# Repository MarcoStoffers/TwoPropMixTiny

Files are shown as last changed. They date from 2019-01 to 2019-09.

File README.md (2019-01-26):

# TwoPropMixTiny
## 2-prop mixer for RC model with 2 drive props, rudder and bow thruster
TwoPropMixTiny

- Depending on the direction, the curve inner motor is braked or controlled to reverse (adjustable via a setup). The sensitivity at which curve position the mixer should intervene can be set via a potentiometer.
- If a bow thruster is also used, this can also be used to support cornering (can also be switched on via setup). Up to which speed the bow thruster intervenes can be adjusted with the 2nd potentiometer.

## Requirement
- All motors (right-hand drive, left-hand drive, bow thruster) must have their own speed controller and the two drives must run equally (the model does not pull away to one side when driving straight ahead).
- The model can be "normally" driven via an RC remote control (Forward | Reverse | Left | Right | Bow Thruster Left | Bow Thruster Right)
- The power supply for the module (4.5V - 5.5V) is guaranteed (see manual / only german at the moment).

## Base
The module is based on a microchip ATtiny841 which is programmed via the [Arduino IDE](https://arduino.cc/). To use the microcontroller, the extension of [Spence Konde](https://github.com/SpenceKonde/ATTinyCore) is necessary. Programming is done without a bootloader directly via the ISP contacts on the bottom side of the PCB with an AVR programmer.

## License
The project is licensed under the Creative Common License. A rebuild for private or non-profit associations is desired, commercial rebuild or distribution I forbid. If someone should develop the mixer further, I ask for the naming of the original project.

CreativeCommonLicense

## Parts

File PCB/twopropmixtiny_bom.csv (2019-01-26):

Qty | Value | Device | Package | Parts | Description
8 |  | JP2EJP2_OHNE_TEXT | JP2 | JP1, JP2, JP3, JP4, JP5, JP6, JP7, JP8 | JUMPER
1 |  | LEDCHIPLED_0805 | CHIPLED_0805 | LED1 | LED
3 |  | SJ | SJ | SJ1, SJ2, SJ3 | SMD solder JUMPER
2 |  | TRIM_EU-PT10 | PT-10 | R17, R18 | POTENTIOMETER
1 | 100nF | C-EUC0805 | C0805 | C1 | CAPACITOR, European symbol
1 | 100µF / 16V | CPOL-EUD | PANASONIC_D | C2 | POLARIZED CAPACITOR, European symbol
9 | 10k | R-EU_R0805 | R0805 | R1, R9, R10, R11, R12, R13, R14, R15, R16 | RESISTOR, European symbol
5 | 1k | R-EU_R0805 | R0805 | R2, R3, R6, R7, R8 | RESISTOR, European symbol
1 | ATtiny841-SSU | TINY24/44/84-SSU | SOIC14 | IC2
4 | IRLML2502 | IRLML2502 | SOT23-3 | Q1, Q2, Q3, Q4 | International Rectifier
1 | ISP | ISP | ISP | U$1
1 | POLOLU2121 | POLOLU2121 | POLOLU2121 | IC1

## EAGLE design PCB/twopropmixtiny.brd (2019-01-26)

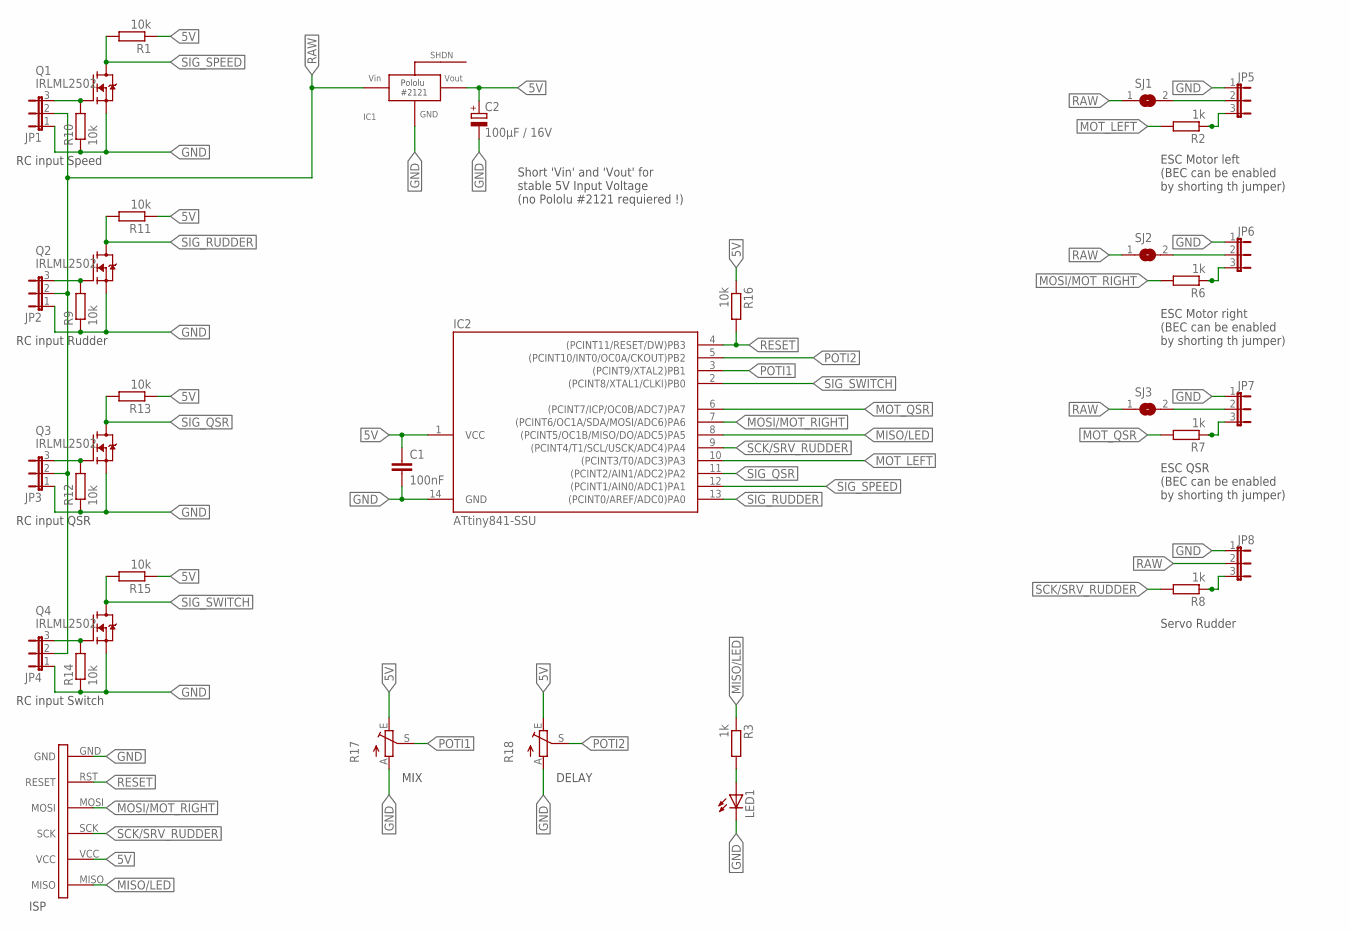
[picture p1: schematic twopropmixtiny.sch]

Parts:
C1: 100nF; C0805
C2: 100µF / 16V; PANASONIC_D
IC1: POLOLU2121
IC2: ATtiny841-SSU; SOIC14
JP1, JP2, JP3, JP4, JP5, JP6, JP7, JP8: JP2EJP2_OHNE_TEXT; JP2
LED1: LEDCHIPLED_0805; CHIPLED_0805
Q1, Q2, Q3, Q4: IRLML2502; SOT23-3
R1, R9, R10, R11, R12, R13, R14, R15, R16: 10k; R0805
R2, R3, R6, R7, R8: 1k; R0805
R17, R18: TRIM_EU-PT10; PT-10
SJ1, SJ2, SJ3: SJ
U$1: ISP

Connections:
5V: C1.1, C2.+, IC1.VOUT, IC2.1 (VCC), R1.1, R11.1, R13.1, R15.1, R16.1, R17.E, R18.E, U$1.VCC
GND: C1.2, C2.-, IC1.GND, IC2.14 (GND), JP1.1, JP2.1, JP3.1, JP4.1, JP5.1, JP6.1, JP7.1, JP8.1, LED1.C, Q1.2 (S), Q2.2 (S), Q3.2 (S), Q4.2 (S), R9.1, R10.1, R12.1, R14.1, R17.A, R18.A, U$1.GND
MISO/LED: IC2.8 ((PCINT5/OC1B/MISO/DO/ADC5)PA5), R3.1, U$1.MISO
MOSI/MOT_RIGHT: IC2.7 ((PCINT6/OC1A/SDA/MOSI/ADC6)PA6), R6.2, U$1.MOSI
MOT_LEFT: IC2.10 ((PCINT3/T0/ADC3)PA3), R2.2
MOT_QSR: IC2.6 ((PCINT7/ICP/OC0B/ADC7)PA7), R7.2
unnamed: JP1.3, Q1.1 (G), R10.2
unnamed: JP5.3, R2.1
unnamed: JP2.3, Q2.1 (G), R9.2
unnamed: LED1.A, R3.2
unnamed: JP3.3, Q3.1 (G), R12.2
unnamed: JP6.3, R6.1
unnamed: JP7.3, R7.1
unnamed: JP8.3, R8.1
unnamed: JP5.2, SJ1.2
unnamed: JP6.2, SJ2.2
unnamed: JP7.2, SJ3.2
unnamed: JP4.3, Q4.1 (G), R14.2
POTI1: IC2.3 ((PCINT9/XTAL2)PB1), R17.S
POTI2: IC2.5 ((PCINT10/INT0/OC0A/CKOUT)PB2), R18.S
RAW: IC1.VIN, JP1.2, JP2.2, JP3.2, JP4.2, JP8.2, SJ1.1, SJ2.1, SJ3.1
RESET: IC2.4 ((PCINT11/RESET/DW)PB3), R16.2, U$1.RST (RESET)
SCK/SRV_RUDDER: IC2.9 ((PCINT4/T1/SCL/USCK/ADC4)PA4), R8.2, U$1.SCK
SIG_QSR: IC2.11 ((PCINT2/AIN1/ADC2)PA2), Q3.3 (D), R13.2
SIG_RUDDER: IC2.13 ((PCINT0/AREF/ADC0)PA0), Q2.3 (D), R11.2
SIG_SPEED: IC2.12 ((PCINT1/AIN0/ADC1)PA1), Q1.3 (D), R1.2
SIG_SWITCH: IC2.2 ((PCINT8/XTAL1/CLKI)PB0), Q4.3 (D), R15.2

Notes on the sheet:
RC input Speed
RC input Rudder
RC input QSR
RC input Switch
ISP
Short 'Vin' and 'Vout' for stable 5V Input Voltage (no Pololu #2121 requiered !)
MIX
DELAY
ESC Motor left (BEC can be enabled by shorting th jumper)
ESC Motor right (BEC can be enabled by shorting th jumper)
ESC QSR (BEC can be enabled by shorting th jumper)
Servo Rudder

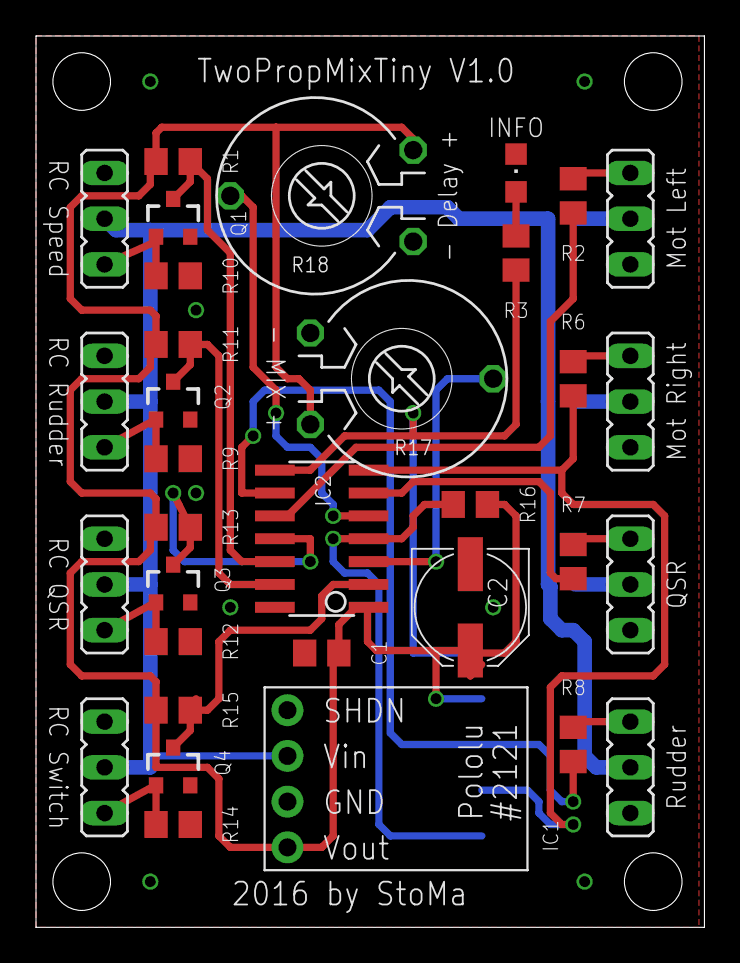
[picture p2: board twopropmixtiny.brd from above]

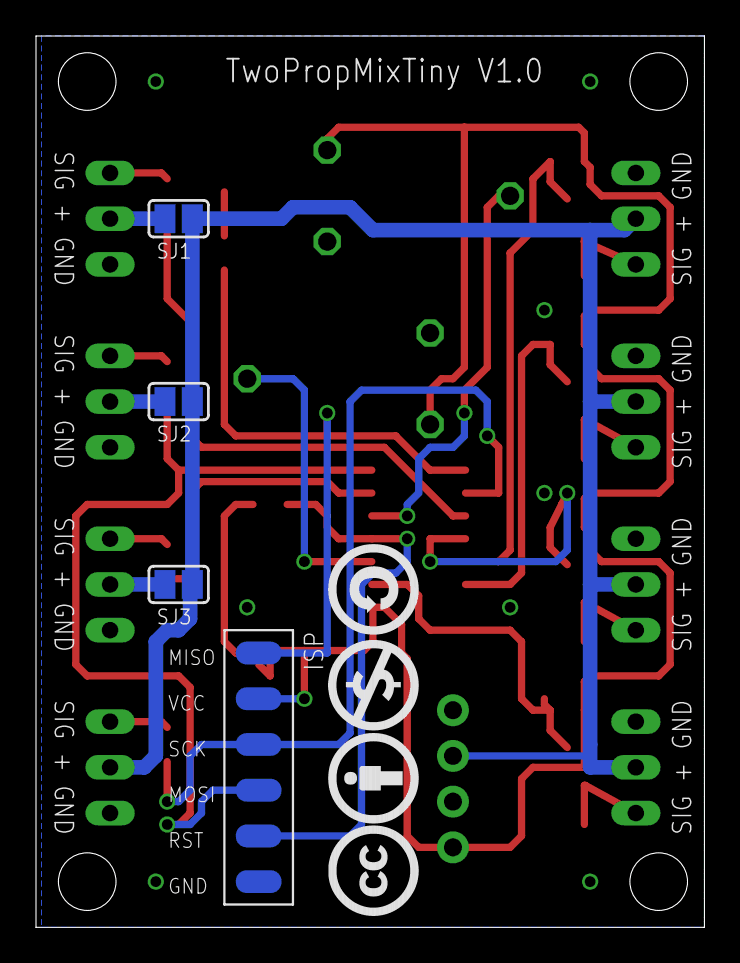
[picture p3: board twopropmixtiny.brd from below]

Board: 2 copper layers, 37.1 x 49.5 mm, 37 parts (4 on the bottom side), 27 nets.

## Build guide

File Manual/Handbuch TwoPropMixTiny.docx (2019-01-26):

Handbuch

TwoPropMixTiny

Version 1.0

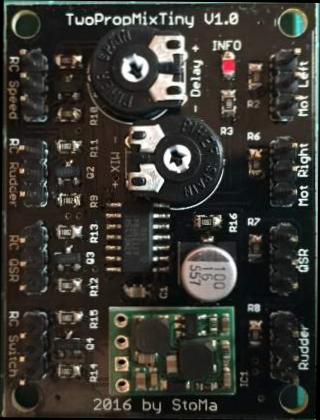
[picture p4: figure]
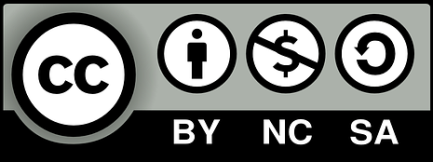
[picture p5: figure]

Inhalt

- Funktion und Einsatzzweck ……………………………………………………………….. Seite 3
- Vorgaben auf Sender & Empfängerseite …………………………………………. Seite 3
- Stromversorgung und Inbetriebnahme ………………………………………..... Seite 4
- Einstellungen und Kalibrieren …………………………………………………………. Seite 6
- Funktion im fahrenden Modell ……………………………………………………….. Seite 7
- Besonderheiten ………………………………………………………………………………… Seite 8

Begriffe und Abkürzungen die in diesem Handbuch verwendet werden:

- QSR (Querstrahlruder) : Quer-Antrieb im Bug eines Schiffes zum besseren Manövrieren
- Schrauben : Antriebsschrauben unter dem Modell
- Motoren : Antriebsmotoren / Elektromotoren
- Brushed / Brushless : Bürstenmotor (herkömmliche Bauweise) / Bürstenloser Motor
- Regler : Fahrtregler (genauer: Fahrtsteller) der die Elektromotoren ansteuert
- FS (Fernsteuerung/Sender) : Funkfernsteuerung mit mind. 4 Kanälen
- BB / ST (Backbord / Steuerbord) : Richtung im Schiffsverkehr (BB = links & ST = rechts)
- BEC : Stromversorgung des Empfängers im Modell über einen Fahrtregler
- UBEC : getrennte, geregelte Stromversorgung des Empfängers aus einem separaten Akku

Funktion und Einsatzzweck

Der TwoPropMixTiny stellt einen Mischer für 2 Antriebsmotoren, einem Querstrahlruder und einem oder mehrere Ruder dar. Über das Setup sind verschiedene Einstellungen zur Anpassung an das Modell möglich und über die beiden Drehregler auf der Platine kann man die Verzögerung (ab welcher Ruderlage soll das Mischen erfolgen) und Mischung (bis zu welcher Geschwindigkeit – abhängig vom Gashebel – soll das Querstrahlruder mit eingemischt werden) jederzeit verändern (auch bei eingeschalteten Modell!).

Die Mischung der 2 Antriebsmotoren und wahlweise des Querstrahlruders ist hilfreich, um große, lange Modelle eine bessere Manövrier-Eigenschaft zu geben. Dazu wird der kurveninnere Motor gedrosselt bis zum Stillstand oder sogar in der Drehrichtung umgedreht (abhängig von den Einstellungen). Diese Drosselung erfolgt proportional zur Ruderlage. Das bedeutet: bisschen Ruder Backbord – Backbord Motor wird ein wenig gedrosselt. Hart Ruder Backbord – Backbord Motor wird gestoppt oder läuft 50% rückwärts.

Zusätzlich kann das Querstrahlruder bis zu einer eingestellten Motor Leistung mit zugemischt werden. Gerade beim Manövrieren in einer Hafenanlage oder bei Anlegen am Kai ist diese Funktion sehr hilfreich. Ist die Funktion abgeschaltet (über den Schalteingang auch über die Fernsteuerung zu- und abschaltbar) wird das Querstrahlruder wie gewohnt mit dem Geber an der Fernsteuerung geregelt.

Wird keine Fahrt vorwärts oder rückwärts über den Gas Hebel an der Fernsteuerung gegeben, kann man mit dem Betätigen des Ruder Hebels ein Drehen des Modells erreichen („Drehen auf dem Teller“). Dieses erfolgt durch gegenseitiges Drehen der Antriebsschrauben und mit Querstrahlruder Unterstützung, wenn die Funktion aktiviert wurde. Auch hier folgt die Drehzahl der Motoren dem Ruderausschlag / Hebelstellung am Sender.

Vorgaben auf Sender & Empfängerseite

Folgende Vorgaben sind mit der Verwendung des TwoPropMixTiny einzuhalten:

- Jeder Motor/QSR hat seinen eigenen Regler und ist funktionsfähig
- Die verbauten Servos sind Standard und keine BUS-Servos (z.B. S-bus von Futaba)
- Der Empfänger wird mit einer Spannung zwischen 4-12V, über das BEC eines Fahrtreglers oder ein gesondertes UBEC betrieben
- Idealerweise sind die Kanäle für Motor, Servo und QSR auf der Senderseite nicht auf Reverse geschaltet

Stromversorgung und Inbetriebnahme

Achtung ! Dieser Abschnitt ist extrem wichtig, da bei einer falschen Stromversorgung der TwoPropMixTiny Schaden nehmen kann. Lesen Sie daher den folgenden Abschnitt genau durch!

Der TwoPropMixTiny wird mit dem Empfänger verbunden und bezieht daher auch seinen Strom. Daher müssen wir anhand der Stromversorgung des Empfängers entscheiden, welche Maßnahmen für die Inbetriebnahme am TwoPropMixTiny nötig sind.

1. Der Empfänger wird über einen der Fahrtregler mit Strom versorgt - BEC (5V) :

Hierzu muss auf der Unterseite der Platine des Mischers eine der Stromversorgungsbrücken SJ1 – SJ3 mit Hilfe eines Lötkolbens und Lot geschlossen werden.

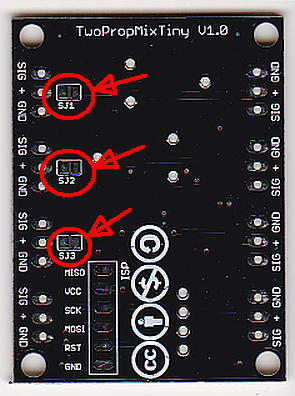
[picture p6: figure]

Soll die Stromversorgung über den Regler

des BB Motors erfolgen, ist SJ1 zu

schließen.

Für den Regler des ST Motors ist

SJ2 zu schließen.

Für den Regler des QSR ist SJ3 zu schließen

Zusätzlich muss auf der Vorderseite eine Kabel-

Brücke eingelötet werden. Im Feld „Pololu

#2121“ sind die beiden Kontakte „Vin“ und

„Vout“ mit einem kleinen Stück Kabel zu

verbinden.

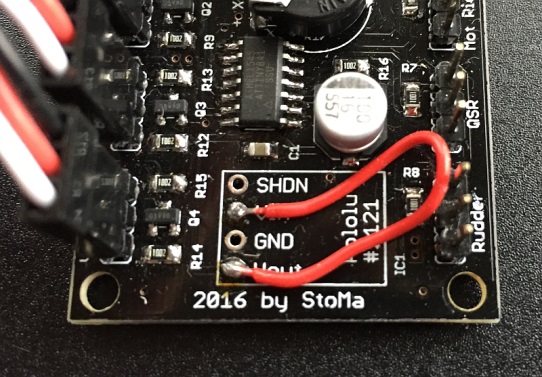
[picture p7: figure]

ACHTUNG ! Gibt das BEC des Fahrtreglers mehr als 5,5V aus muss Variante 3 gewählt werden !

2. Der Empfänger wird mit einem separaten UBEC mit Strom versorgt:

Hierzu bleiben die Brücken SJ1 – SJ3 auf der Unterseite des Mischers offen. Die Kabelbrücke muss auch hier eingelötet werden

ACHTUNG ! Gibt das externe UBEC mehr als 5,5V aus muss Variante 3 gewählt werden !

3. Der Empfänger wird mit einem separaten Akku oder einem (U)BEC mit mehr als 5,5V betrieben:

Hier bleiben die Brücken auf der Unterseite der Platine ebenfalls geöffnet. Zusätzlich wird ein Spannungsregler vom Typ Pololu #2121 benötigt. Dieser ist über die einschlägigen Onlineshops oder Auktionsportale zu beziehen.

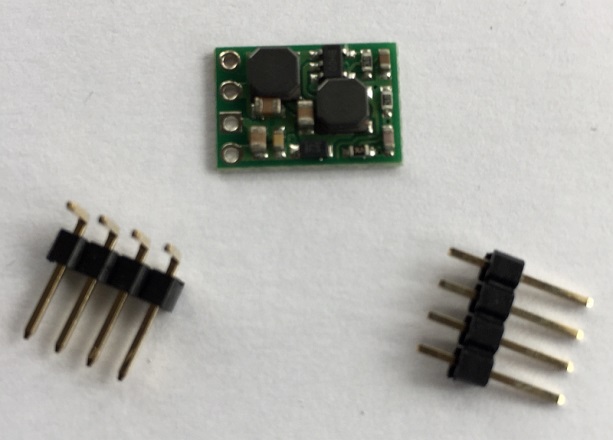
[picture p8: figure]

Zur Montage wird die abgewinkelte Stiftleiste mit dem langen Ende von unten durch die Platine gesteckt und der Spannungsregler von oben aufgesteckt und verlötet

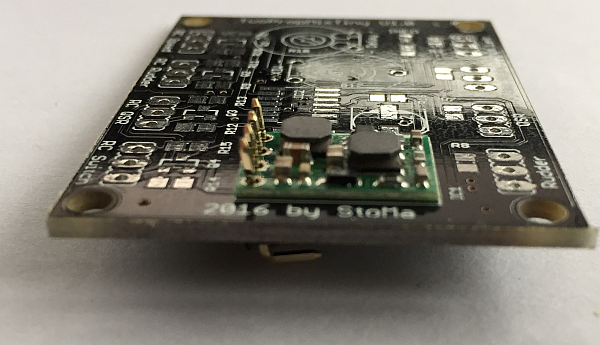
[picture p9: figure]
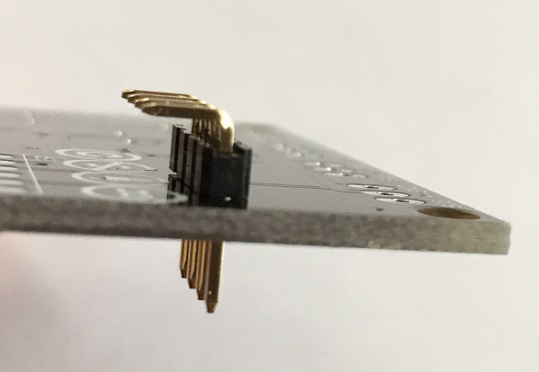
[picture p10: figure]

Die überstehenden Kontakte dann bitte mit einem feinen Seitenschneider entfernen oder zumindest isolieren. Mit diesem Modul kann der Empfänger mit nachgeschalteten TwoPropMixTiny zwischen 4V und 12V betrieben werden.

Inbetriebnahme

Für den Anschluss des Mischers an den Empfänger eignen sich kurze Anschlusskabel für Servos in der Länge 10cm. Die Belegung der Servokabel ist wie folgt:

- Schwarz = Minus (GND)
- Rot = Plus (+)
- Weiß = Signal (SIG)

Die Pinbelegung ist auf der Unterseite der Platine aufgedruckt. Der entspr. Eingang ist wiederrum aus Platzgründen auf der Oberseite aufgedruckt.

- Der Eingang „RC Rudder“ wird an dem Empfänger Port für das Ruder angeschlossen. Der Servo für das Ruder wird am Ausgang „Rudder“ eingesteckt.
- Der Motoranschluss vom Empfänger kommt an „RC Speed“ und die beiden Fahrtregler der Motoren an „Mot Left“ bzw. „Mot Right“.
- Empfängerausgang für das QSR kommt an „RC QSR“ und der Regler vom QSR an den Ausgang „QSR“

Der Anschluss „RC Schwitch“ ist etwas Besonderes. Man kann Ihn entweder über einen Schaltkanal direkt mit dem Empfänger verbinden oder den Pin „SIG“ an einem Multiswitch Port schalten (gegen Minus (GND) schalten). Welchen Typ von Eingang der „RC Switch“ Port erhalten soll, wird im Setup eingestellt!

Einstellungen und Kalibrieren

Um den TwoPropMixTiny an das jeweilige Modell und Fernsteuerung anzupassen gibt es ein Setup welches mit dem Hebel an der Fernsteuerung für den Motor und der „Info“ LED auf der Platine durchgeführt wird. Zur Vorsicht bitte das Setup nur mit nicht angesteckten Fahrtenregler und Servo vornehmen. Die Ausgabe der Signale ist zwar deaktiviert aber einige Fahrtregler interpretieren das fehlende Signal als Failsafe und gehen dann gerne mal in eine Vollgas Stellung.

Das Setup geschieht folgendermaßen:

- Beim Einschalten des Empfängers den Knüppel für den Motor am Sender auf Vollgas vorwärts stellen und halten (ist hier ein Reverse programmiert natürlich auf rückwärts)
- Die LED auf dem Mischer blinkt 1x
- Hebel wieder in Mittelstellung -> die LED blinkt noch einmal kurz auf
- Wenn der Hebel jetzt wieder auf Vollgas vorwärts gebracht wird, ist der Schaltkanal für das Zuschalten der QSR Unterstützung, als RC-Eingang programmiert. Wird der Hebel auf Vollgas rückwärts gestellt, ist der Schaltkanal ein normaler Schalteingang, welcher mit einem Schaltmodul oder Multiswitch beschaltet werden muss -> zur Bestätigung blinkt die LED 2x
- Hebel wieder in Mittelstellung -> die LED blinkt einmal kurz auf
- Beim nächsten Schritt wird per „vorwärts“ Richtung des Hebels der Enhanced Mode aktiviert, bei dem der Kurven innere Motor nicht nur bis zum Stillstand sondern bis 50% Rückwärtsfahrt angesteuert wird. Hebel rückwärts deaktiviert den Enhanced Mode -> zur Bestätigung blinkt die LED 3x
- Hebel wieder in Mittelstellung -> die LED blinkt einmal kurz auf
- Im letzten Schritt kann man den Mischer mit „Hebel vorwärts“ in den Reverse Mode versetzen. Damit werden die Motoren vertauscht und das QSR dreht in die andere Richtung. Dieses wird benötigt wenn an der Fernsteuerung Kanäle auf reverse geschaltet werden mussten, da der Einbau von z.B. Ruderservo nicht anders möglich war. „Hebel rückwärts“ übernimmt den Standard Mode. -> zur Bestätigung blinkt die LED 4x
- Hebel wieder in Mittelstellung -> die LED blinkt einmal kurz auf
- Das Setup ist abgeschlossen und der Mischer läuft normal los

Um den Mischer an die unterschiedlichen Fernsteuerungen anzupassen, gibt es eine Kalibrierung. Dazu den Empfänger wieder ausschalten, den Motor Hebel an der Fernsteuerung auf Vollgas rückwärts bringen und den Empfänger wieder einschalten. Die „Info“ LED auf dem TwoPropMixTiny blinkt nun dauerhaft für etwa eine Minute. In dieser Minute müssen die verwendeten Hebel an der Fernsteuerung für Motor, Lenkung, QSR und wenn programmiert auch den Schalteingang auf Maximum und Minimum gebracht werden. Also am besten mit dem Motorhebel anfangen:

Max, 1s warten, Min, 1s warten – weiter zur Lenkung: Max, 1s warten, Min, 1s warten und so weiter. Dieser Vorgang kann jederzeit wiederholt werden. Nach dem Blinken der LED werden die Werte in den internen Speicher vom Mischer abgelegt. Auch die Einstellungen aus dem Setup werden dauerhaft gespeichert, können aber jederzeit wieder geändert werden in dem das Setup wiederholt wird.

Die Einstellung der beiden Drehregler für „Delay“ – ab welcher Ruderlage das Abbremsen des kurveninneren Motors erfolgen soll – und „Mix“ – bis zu welcher Geschwindigkeit das QSR mit dazu gemischt werden soll – nimmt man am Besten im fahrbereiten Modell vor. Für die Verstellung der Drehregler eignet sich ein billiger Phasenprüfer aus dem Baumarkt.

Funktionen im fahrenden Modell

Der TwoPropMixTiny unterstützt die Fahrfunktion im Modell bei unterschiedlichen Situationen

- Fahrt voraus ohne QSR Unterstützung

Bei Fahrt voraus (vorwärts) wird ab der eingestellten Verzögerung der Ruderlage (Drehregler „Delay“) der kurveninnere Motor gedrosselt bis er bei hart Ruder zum Stillstand / 50% rückwärts dreht (je nach Einstellung im Setup). Dadurch ist ein großes, langes Modell besser zu manövrieren.

Ist der Drehregler „Delay“ auf Vollanschlag „+“ ist diese Funktion deaktiviert!

- Fahrt voraus mit QSR Unterstützung

Ist die QSR Unterstützung aktiv, wird bis zu der eingestellten Gashebel-Position (über den Drehregler „Mix“) das QSR je nach Ruderlage bi zur maximalen Drehzahl bei hart Ruder zu gemischt. Auf die Funktion für das verlangsamen der kurveninneren Schraube hat dies keinen Einfluss.

Ist der Drehregler „Mix“ auf Vollanschlag „+“ läuft das QSR bei dieser Funktion in jeder Kurvenfahrt mit!

- Fahrt achtern ohne QSR Unterstützung

Die Rückwärtsfahrt wird nicht beeinflusst. Die beiden Antriebsmotoren laufen 1:1 analog zum Gashebel an der Fernsteuerung

- Fahrt achtern mit QSR Unterstützung

Auch hier wird nur die QSR Unterstützung hinzugeschaltet. Andere Funktionen bleiben erhalten.

- Betätigung des Ruder-Hebels bei stehenden Modell ohne QSR Unterstützung

Wird bei stehenden Modell der Ruder-Hebel bewegt, werden die Antriebsmotoren gegenläufig angesteuert (vorwärts & rückwärts) so dass sich das Modell auf der Stelle dreht. Die Geschwindigkeit der Motoren ist abhängig von der Ruderlage – bei hart Ruder drehen die Motoren mit der maximalen Drehzahl

- Betätigung des Ruder-Hebels bei stehenden Modell mit QSR Unterstützung

Gleiche Funktion wie oben nur durch die Unterstützung mit dem QSR dreht das Modell quasi auf dem Teller (Drehachse ist mittig vom Schiff – nicht achtern).

Besonderheiten

Es gibt ein paar Punkte die man bei dem Einsatz des TwoPropMixTiny wissen sollte:

- Nach dem Einschalten des Empfängers wird erst auf gültige Werte gewartet biss der Start des Mischers erfolgt. Dies ist für den Einsatz des TwoPropMixTiny mit einem 2.4GHz Empfänger wichtig, da hier erst noch die Verbindung zum Sender hergestellt werden muss (Binding) was gerne mal 1-2 s dauert.
- Nach dem Start des Mischers werden von den Eingängen „RC Speed“, „RC Rudder“ & „RC QSR“ die Mittelstellung übernommen. Verwendet man am Sender für diese Kanäle einen Hebel, der nicht automatisch in die Mittelstellung zurück geht (nicht selbst neutralisierender Hebel / Ratsche), wird die zuletzt eingestellte Position als Mittelstellung gespeichert. Hier hilft dann nur ein Neustart durch Aus- und wieder Einschalten des Modells bei korrigierter Hebelstellung!
- Verwendet man Fahrtregler, die bei Rückwärtsfahrt nur 50% Leistung ausgeben, um das Modell nicht unter Wasser zu ziehen, wird das Modell nicht auf der Stelle drehen können.

Auch ist der Effekt im Enhanced Mode nicht so stark wie bei voller Leistung rückwärts.

- Bei der Verwendung von Brushless Motoren ist der Start des Motors meist recht ruckig. Hier sollte der Enhanced Mode – also das rückwärts drehen des kurveninneren Motors – nicht aktiviert werden, da es sonst zu unschönen Fahrmanövern kommt.

Marco Stoffers Handbuch TwoPropMixTiny 11/2016

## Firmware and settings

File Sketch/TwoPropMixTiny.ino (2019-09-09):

/* ==========================================================================
**  TwoPropMixTiny V1.1 
**
**  Core: ATtiny841 / Dr.Azzy (http://drazzy.com/e/tiny841.shtml9)
**
** Setup:
** ------
** 1) Motor stick in max up-position and switch on -> wait for long LED blink
** 2) Motor stick in center-position -> wait for LED blink
** 3) Motor stick in up-position for RC Switch input or down-position for Switch input via Multiswitch -> wait for double LED blink
** 4) Motor stick in center-position -> wait for LED blink
** 5) Motor stick in up-position for Enhanced mode on or down-position for Enhanced mode off -> wait for tripple LED blink
** 6) Motor stick in center-position -> wait for LED blink
** 7) Motor stick in up-position for Reverse mode or down-position for Normal mode -> wait for 4 times LED blink
** 8) Motor stick in center-position -> wait for long LED blink
** Done !
**
** Calibration: 
** ------------
** 1) Motor stick in max down-position and switch on -> wait for LED permanent blinking (1min)
** 2) Put all sticks to their maximum and minimum positions one after another until LED blinking stops
** Done !
**
**  D3 : QSR Output
**  D4 : Motor right Output
**  D6 : Rudder Output
**  D7 : Motor left Output
**  D5 : LED Output
**
**  D0 : RC Input for Switch
**  D8 : RC Input for QSR
**  D9 : RC Input for Motor
**  D10: RC Input for Rudder
**
**  A10: Poti Delay
**  A08: Poti Mix
**
**  EEPROM address:
**  00 - reserved for calibrating value OSCAL
**  01 - 1 for RC-Switch / 0 for digital Switch Input
**  02 - 1 for enhanced Mode on / 0 for off
**  03 - 1 for Reverse / 0 Normal
**  04 - 1 for calibration done / 0 for uncalibrated
**  10 - max value for RCrudder
**  12 - min value for RCrudder
**  14 - max value for RCmotor
**  16 - min value for RCmotor
**  18 - max value for RCqsr
**  20 - min value for RCqsr
**
** Author: Marco Stoffers
** Year: 2016
** License: CC (BY|NC|SA)
** -------------------------------------------------------------------------*/
#include <EEPROM.h>
// -----------------------------
// defines
// -----------------------------
#define RUDDER_PIN 6 
#define MOTORL_PIN 7
#define MOTORR_PIN 4
#define QSR_PIN 3

#define RC_RUDDER_PIN 10
#define RC_MOTOR_PIN 9
#define RC_QSR_PIN 8
#define RC_SWITCH_PIN 0

#define LED_PIN 5

#define POTI1_PIN A10
#define POTI2_PIN A8

#define between(x, a, b)  (((a) <= (x)) && ((x) <= (b)))
// -----------------------------
// variables
// -----------------------------
// the helper variables
uint8_t i = 0;
uint8_t j = 0;
// First the Array of all pins
volatile uint8_t pin_array[11] { RUDDER_PIN, MOTORL_PIN, MOTORR_PIN, QSR_PIN, LED_PIN, RC_RUDDER_PIN, RC_MOTOR_PIN, RC_QSR_PIN, RC_SWITCH_PIN, POTI1_PIN, POTI2_PIN };
// 2 arrays with times for the RC Measurement and one for Measurement done or not
volatile unsigned long start_micros[4]; // Rudder, Motor, QSR, Switch
volatile unsigned long stop_micros[4];
volatile boolean measurement[4] { false, false, false, false };
// temporary stored rc values for building the average over 3 times
volatile uint16_t rc_temp[4];    // Rudder, Motor, QSR, Switch
volatile uint16_t rc_value[4] {0, 0, 0, 0};
volatile uint8_t rc_avg_count[4];
// array for storing the rc signal quality (ok/bad)
volatile boolean rc_ok[4] {false, false, false, false};    // Rudder, Motor, QSR, Switch
volatile boolean rc_switch_enable;
// the middle, max and min of the rc signals as an array (will be overwritten by reading the eeprom)
uint16_t rc_middle[3] {1500, 1500, 1500};
uint16_t rc_max[3] { 1500, 1500, 1500 };    // Rudder, Motor, QSR
uint16_t rc_min[3] { 1500, 1500, 1500 };    // Rudder, Motor, QSR
// set the output array so there are all ESC on neutral
uint16_t output_value[3] {1500, 1500, 1500};
// different variables for calculating the mix level
boolean mix = true;
uint16_t mix_value = 0;
uint16_t delay_value = 0;
uint16_t helper = 0;
boolean switch_value = false;
boolean enhanced_mode = false;
uint16_t rc_enhanced_value;
uint8_t loop_count = 0;
boolean turn_table = true;
boolean reverse = false;
uint16_t calib_temp;
uint16_t qsr_temp = 0;

// -----------------------------
// Setup
// -----------------------------
void setup() {
    for(i = 0; i < 5; i++) {                    // set the first 4 Pins in the array
        pinMode(pin_array[i], OUTPUT);          // to outputs
        digitalWrite(pin_array[i], LOW);        // and set them low / off (Servo Pins)
    }
    for(i = 5; i < 11; i++) {                   // set the next 6 Pins in the array
        pinMode(pin_array[i], INPUT);           // to inputs
    }

    start_rc_input();                           // start RC input via PinChange Interrupt
    delay(500);
    while(!rc_ok[0] && !rc_ok[1] && !rc_ok[2]) {  }            // ... wait until RC-signals are stable
    delay(500);
    if(rc_value[1] > 1700) do_setup();          // if Motor stick is in in position 'forward' go to setup
    if(rc_value[1] < 1300) do_calibrate();      // if Motor stick in in in position 'backward' go to calibration
    
    if(EEPROM.read(3) > 0) {                    // if module is already calibrated
        for(i=0; i<3; i++) {
            rc_max[i]=eeprom_read(10+(i*4));    // load values from eeprom
            rc_min[i]=eeprom_read(12+(i*4));
        }
    }
    else {                                      // if not ...
        for(i=0; i<3; i++) {
            rc_max[i] = 1900;                   // store default values
            rc_min[i] = 1100;
        }
    }
    
    if(EEPROM.read(1) > 0) {                    // read EEPROM and check if RC switch is stored as enabled
      rc_switch_enable = true;
      start_rc_switch_input();                  // and switch on Interrupt for Switch RC
    }
    else {                                      // otherwise set PIN to Input with Pullup Resistor enabled
      rc_switch_enable = false;
      pinMode(RC_SWITCH_PIN, INPUT_PULLUP); 
    }

    if(EEPROM.read(2) > 0) enhanced_mode = true;  // read EEPROM and check if Enhanced Mode is stored as enabled
    else enhanced_mode = false;                 // otherwise disable Enhanced Mode

    learn_rc_middle();                          // now learn middle position of Rudder & Motor stick
        
    start_servos();                             // ... start servos
    output();                                   // ... give first incomming positions to servos

    if(EEPROM.read(4) == 1) reverse = true;     // if module is setup for reverse set variable
    else reverse = false;

    rc_enhanced_value = (rc_middle[1] - rc_min[1]) / 2;   // 50% reverse at enhanced mode

    led_on();                                   // ... and switch LED on to show valid RC signals and Servo output    
}

// -----------------------------
// Main loop
// -----------------------------
void loop() {

    mix_value = map(analogRead(POTI1_PIN),0,1024,0,(rc_max[1] - rc_middle[1]));                 // get values from the potis and map it into rc range
    delay_value = map(analogRead(POTI2_PIN),0,1024,0,(rc_max[0] - rc_middle[0]));
    if(delay_value > (rc_max[0] - rc_middle[0] - 20)) mix = false;                              // if delay poti is set to max, disable two prop mixing during drive
    else mix = true;
    if(!rc_switch_enable) switch_value = !digitalRead(RC_SWITCH_PIN);                           // if switch input is set to rc read it otherwise read digital input
    else {
      if(rc_value[3] > 1700) switch_value = true;                                               
      else switch_value = false;
    }
    
    //
    // Calculate Mixing Level
    //
    //     forward
    //    ---------
    if(rc_ok[0] && rc_ok[1] && (rc_value[1] > (rc_middle[1]+20))) {
        //
        // Rudder mix only if given value (poti "delay") is below max
        //    left
        //   -------
        if(rc_value[0] > (rc_middle[0]+delay_value)) {
            
            if(mix && !enhanced_mode) helper = map(rc_value[0],(rc_middle[0]+delay_value),rc_max[0],0,(rc_max[1] - rc_middle[1]));
            else if(mix && enhanced_mode) helper = map(rc_value[0],(rc_middle[0]+delay_value),rc_max[0],0,(rc_max[1] - rc_middle[1] + rc_enhanced_value));
            else helper = rc_value[1];
            if(reverse) {
                output_value[0] = rc_value[1];
                output_value[1] = rc_value[1] - helper;
                if(!enhanced_mode && (output_value[1] < rc_middle[1])) output_value[1] = rc_middle[1];
                if(enhanced_mode && (output_value[1] < (rc_middle[1] - rc_enhanced_value))) output_value[1] = rc_middle[1] - rc_enhanced_value;
            }
            else {
                output_value[1] = rc_value[1];
                output_value[0] = rc_value[1] - helper;
                if(!enhanced_mode && (output_value[0] < rc_middle[1])) output_value[0] = rc_middle[1];
                if(enhanced_mode && (output_value[0] < (rc_middle[1] - rc_enhanced_value))) output_value[0] = rc_middle[1] - rc_enhanced_value;
            }
            turn_table = false;
        }
        else {
          if(reverse) output_value[1] = rc_value[1];
          else output_value[0] = rc_value[1];
        }
        //
        //    right
        //   ------
        if(rc_value[0] < (rc_middle[0]-delay_value)) {
            if(mix && !enhanced_mode) helper = map(rc_value[0],(rc_middle[0]-delay_value),rc_min[0],0,(rc_max[1] - rc_middle[1]));
            else if(mix && enhanced_mode) helper = map(rc_value[0],(rc_middle[0]-delay_value),rc_min[0],0,(rc_max[1] - rc_middle[1] + rc_enhanced_value));
            else helper = rc_value[1];
            if(reverse) {
                output_value[0] = rc_value[1] - helper;
                output_value[1] = rc_value[1];
                if(!enhanced_mode && (output_value[0] < rc_middle[1])) output_value[0] = rc_middle[1];
                if(enhanced_mode && (output_value[0] < (rc_middle[1] - rc_enhanced_value))) output_value[0] = rc_middle[1] - rc_enhanced_value;
            }
            else {
                output_value[1] = rc_value[1] - helper;
                output_value[0] = rc_value[1];
                if(!enhanced_mode && (output_value[1] < rc_middle[1])) output_value[1] = rc_middle[1];
                if(enhanced_mode && (output_value[1] < (rc_middle[1] - rc_enhanced_value))) output_value[1] = rc_middle[1] - rc_enhanced_value;
            }
            turn_table = false;
        }
        else {
          if(reverse) output_value[0] = rc_value[1];
          else output_value[1] = rc_value[1];
        }
        //
        // QSR mix only when switch is on and speed is below given value (poti "mix")
        //
        if(switch_value && rc_ok[2] && (rc_value[1] < (rc_middle[1] + mix_value))) {
            //
            //     right
            //    -------
            if(rc_value[0] > (rc_middle[0]+20)) {
                if(reverse) qsr_temp = rc_middle[2] - (rc_value[0] - rc_middle[0]);
                else qsr_temp = rc_middle[2] + (rc_value[0] - rc_middle[0]);

                if(output_value[2] > qsr_temp) output_value[2]--;
                if(output_value[2] < qsr_temp) output_value[2]++;
            }
            //
            //     left
            //    ------
            else if(rc_value[0] < (rc_middle[0]-20)) {
                if(reverse) qsr_temp = rc_middle[2] + (rc_middle[0] - rc_value[0]);
                else qsr_temp = rc_middle[2] - (rc_middle[0] - rc_value[0]);

                if(output_value[2] > qsr_temp) output_value[2]--;
                if(output_value[2] < qsr_temp) output_value[2]++;
            }
            else {
              if(output_value[2] > rc_middle[2]) output_value[2]--;
              if(output_value[2] < rc_middle[2]) output_value[2]++;
            }
        }
        else {
          if(output_value[2] > rc_middle[2]) output_value[2]--;
          if(output_value[2] < rc_middle[2]) output_value[2]++;
        }
    }
    //
    //     reverse
    //    ---------
    else if(rc_ok[1] && (rc_value[1] < (rc_middle[1]-20))) {
        output_value[1] = rc_value[1];
        output_value[0] = rc_value[1];
        //
        // QSR mix only when switch is on and speed is below given value (poti "mix")
        //
        if(switch_value && rc_ok[2] && ((rc_middle[1] - mix_value) < rc_value[1])) {
            //
            //     right (turn QSR left for reverse)
            //    -----------------------------------
            if(rc_value[0] > (rc_middle[0]+20)) {
                if(reverse) qsr_temp = rc_middle[2] - (rc_middle[0] - rc_value[0]);
                else qsr_temp = rc_middle[2] + (rc_middle[0] - rc_value[0]);

                if(output_value[2] > qsr_temp) output_value[2]--;
                if(output_value[2] < qsr_temp) output_value[2]++;
            }
            //
            //     left (turn QSR right for reverse)
            //    -----------------------------------
            else if(rc_value[0] < (rc_middle[0]-20)) {
                if(reverse) qsr_temp = rc_middle[2] + (rc_value[0] - rc_middle[0]);
                else qsr_temp = rc_middle[2] - (rc_value[0] - rc_middle[0]);

                if(output_value[2] > qsr_temp) output_value[2]--;
                if(output_value[2] < qsr_temp) output_value[2]++;
            }
            else {
              if(output_value[2] > rc_middle[2]) output_value[2]--;
              if(output_value[2] < rc_middle[2]) output_value[2]++;
            }
        }
        else {
          if(output_value[2] > rc_middle[2]) output_value[2]--;
          if(output_value[2] < rc_middle[2]) output_value[2]++;
        }
    }
    else {
        //
        // "Turn on table" if boat is standing still
        //
        //    right
        //   -------
        if(turn_table && (rc_value[0] > (rc_middle[0] + 20)) && between(rc_value[1], rc_middle[1] - 20, rc_middle[1] + 20)) {
            if(reverse) {
                output_value[0] = rc_middle[1] + (rc_value[0] - rc_middle[0]);
                output_value[1] = rc_middle[1] - (rc_value[0] - rc_middle[0]);
                if(switch_value) output_value[2] = rc_middle[2] - (rc_value[0] - rc_middle[0]);
            }
            else {
                output_value[0] = rc_middle[1] - (rc_value[0] - rc_middle[0]);
                output_value[1] = rc_middle[1] + (rc_value[0] - rc_middle[0]);
                if(switch_value) output_value[2] = rc_middle[2] + (rc_value[0] - rc_middle[0]);
            }
            
        }

        //
        //    left
        //   ------
        else if(turn_table && (rc_value[0] < (rc_middle[0] - 20)) && between(rc_value[1], rc_middle[1] - 20, rc_middle[1] + 20)) {
            if(reverse) {
                output_value[0] = rc_middle[1] - (rc_middle[0] - rc_value[0]);
                output_value[1] = rc_middle[1] + (rc_middle[0] - rc_value[0]);
                if(switch_value) output_value[2] = rc_middle[2] + (rc_middle[0] - rc_value[0]);
            }
            else {
                output_value[0] = rc_middle[1] + (rc_middle[0] - rc_value[0]);
                output_value[1] = rc_middle[1] - (rc_middle[0] - rc_value[0]);
                if(switch_value) output_value[2] = rc_middle[2] - (rc_middle[0] - rc_value[0]);
            }
            
        }

        else {
            output_value[0] = rc_middle[1];
            output_value[1] = rc_middle[1];  
            output_value[2] = rc_middle[2]; 
            if(between(rc_value[0],rc_middle[0] - 20, rc_middle[0] +20)) turn_table = true; 
        }
    }
    //
    // QSR normal (will follow RC input QSR) when switch is off
    //
    if(!switch_value) output_value[2] = rc_value[2];
        
    //
    // and give everything to the ouput pins
    //
    output();
}

// -----------------------------
// Switch LED on
// -----------------------------
void led_on() {
    digitalWrite(LED_PIN, HIGH);
}

// -----------------------------
// Switch LED off
// -----------------------------
void led_off() {
    digitalWrite(LED_PIN, LOW);
}

// -----------------------------
// Blink LED short
// -----------------------------
void blink_led_short() {
    digitalWrite(LED_PIN, HIGH);
    delay(200);
    digitalWrite(LED_PIN, LOW);
    delay(200);
}

// -----------------------------
// Blink LED long
// -----------------------------
void blink_led_long() {
    digitalWrite(LED_PIN, HIGH);
    delay(500);
    digitalWrite(LED_PIN, LOW);
    delay(500);
}

// -----------------------------
// Learn Middle for Rudder and Motor
// -----------------------------
void learn_rc_middle() {
    rc_middle[0] = rc_value[0];
    rc_middle[1] = rc_value[1];     
    rc_middle[2] = rc_value[2];
}

// -----------------------------
// Setup Routine
// -----------------------------
void do_setup() {
    delay(500);                         // wait 0,5s to avoid interferences from the FS
    blink_led_long();
    while(!(rc_value[1] < 1700)) { }    // wait until the RC signal gets shorter than 1700ms (stick goes to middle)
    delay(500);                         // wait so that the stick is in middle postion
    blink_led_short();
    delay(500);
    while(!((rc_value[1] < 1300)||(rc_value[1] > 1700))) { }  // wait until the stick will be moved up or down
    delay(300);
    if(rc_value[1] < 1300) {            // if down set Switch Port to normal (no RC signal)
      rc_switch_enable = false;
      EEPROM.write(1, 0);               // and store setting in eeprom
    }
    else { 
      rc_switch_enable = true;          // if up set Switch Port to RC input 
      EEPROM.write(1, 1);               // and store setting in eeprom
    }
    delay(300);
    blink_led_short();                  // two blinks as an "ok"
    blink_led_short();
    delay(300);
    while(!between(rc_value[1],1300,1700)) { }    // again wait for the stick to become middle
    blink_led_short();
    delay(500);
    while(!((rc_value[1] < 1300)||(rc_value[1] > 1700))) { }  // and wait for up or down movement of the stick
    delay(300);
    if(rc_value[1] < 1300) {            // if down disable Enhanced mode
      enhanced_mode = false;
      EEPROM.write(2, 0);               // write setting to eeprom
    }
    else { 
      enhanced_mode = true;             // if up enable Enhanced mode
      EEPROM.write(2, 1);               // write setting to eeprom
    }
    delay(300);
    blink_led_short();                  // three blinks for an "ok"
    blink_led_short();
    blink_led_short();
    while(!between(rc_value[1],1300,1700)) { }  // and as always: wait for stick to become middle
    blink_led_short();
    delay(500);
    while(!((rc_value[1] < 1300)||(rc_value[1] > 1700))) { }    // and wait for up or down movement
    delay(300);
    if(rc_value[1] < 1300) {            // down sets mixing to "normal"
      reverse = false;
      EEPROM.write(4, 0);               // write setting to eeprom
    }
    else { 
      reverse = true;                   // up sets mixing to "reverse"
      EEPROM.write(4, 1);               // write setting to eeprom
    }
    delay(300);
    blink_led_short();                  // four blinks for an "ok" here
    blink_led_short();
    blink_led_short();
    blink_led_short();
    while(!between(rc_value[1],1300,1700)) { }    // and last: wait for stick to set to middle
    blink_led_long();                             // blink once and end setup
    delay(300);
}

// -----------------------------
// Calibration Routine
// -----------------------------
void do_calibrate() {
    delay(500);                                                 // calibration is an timed setup (nearly 10s)
    loop_count = 0;                                             
    while(loop_count < 35) {                                    // count the loops to time the calibration
        blink_led_short();                                      // blink led short on any loop to show calibration is still progress
        for(i=0; i<3; i++) {                                    // go on each rc signal
          calib_temp = rc_value[i];                             // store the actual rc value temporaly
          if(calib_temp > rc_max[i]) rc_max[i] = calib_temp;    // and check if the given rc value (from the receiver) is more or less of the already stored one ...
          if(calib_temp < rc_min[i]) rc_min[i] = calib_temp;    // ... if so store the new one in the array
        }
        loop_count++;
    }
    for(i=0; i<3; i++) {                                        // store the new rc values for max and min in the eeprom cells
        eeprom_write((10+(i*4)),rc_max[i]);
        eeprom_write((12+(i*4)),rc_min[i]);
    }
    EEPROM.write(3, 1);                                         // and write a "one" to the eeprom to show "yes, calibrated"
}

// -----------------------------
// Subroutine: Read EEPROM 16bit
// -----------------------------
uint16_t eeprom_read(uint8_t addr) {                            // simple routine to read 2 8bit eeprom cells into the needed 16bit value
    uint16_t var = ((EEPROM.read(addr+1) << 8 ) | EEPROM.read(addr));
    return var;
}

// -----------------------------
// Subroutine: Write EEPROM 16bit
// -----------------------------
void eeprom_write(uint8_t addr, uint16_t var) {                 // simple routine to store a 16bit value in 2 8bit eeprom cells
    uint8_t help = var;
    EEPROM.write(addr, help);
    help = (var >> 8);
    EEPROM.write(addr+1, help);
}

// -----------------------------
// Output
// -----------------------------
void output() {
    if(rc_ok[0]) OCR1A = rc_value[0];                           // load the OC register (output compare register) with the latest rc signals for output ...
    else OCR1A = rc_middle[0];                                  // ... only if the incomming rc signals are still ok
    if(rc_ok[1]) {
        OCR1B = output_value[0];
        OCR2A = output_value[1];
    }
    if(rc_ok[2]) OCR2B = output_value[2];
}
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

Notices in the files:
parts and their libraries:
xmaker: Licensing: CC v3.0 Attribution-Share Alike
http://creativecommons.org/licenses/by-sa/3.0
